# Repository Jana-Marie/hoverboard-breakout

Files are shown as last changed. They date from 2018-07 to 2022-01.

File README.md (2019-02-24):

# Hoverboard breakout boards

### [Bobbycar breakout](/bobbycar_breakout/)

Hoverboard breakout board for Bobbycars, features a PCB-Nunchuk connector, a linear regulator, pull-ups for I2C and pull-downs for ADC-input

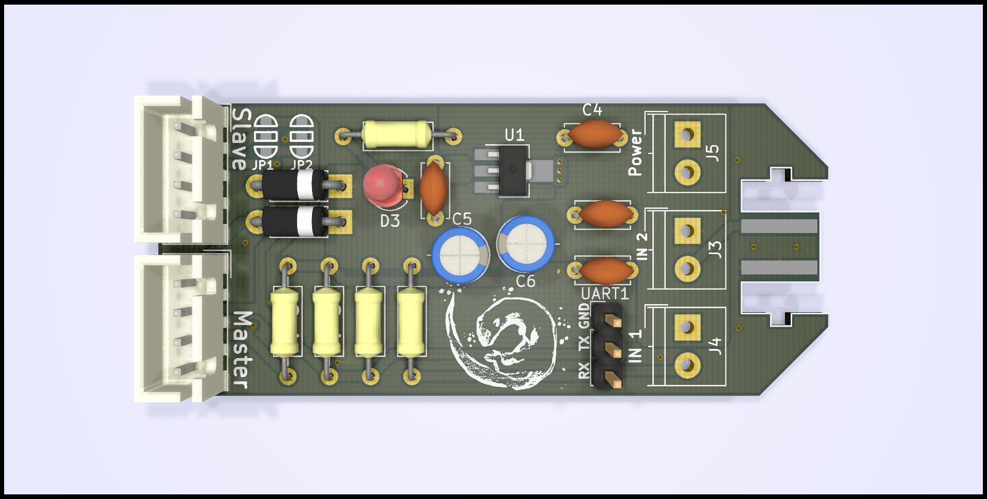
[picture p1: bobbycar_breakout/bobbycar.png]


### [Nunchuk breakout](/nunchuk_breakout/)

Nunchuk to hoverboard connector board, features a Nunchuk socket, a linear regulator and pullups. This board is only intended for nunchuk use, therefore it is smaller and features the fitting socket.

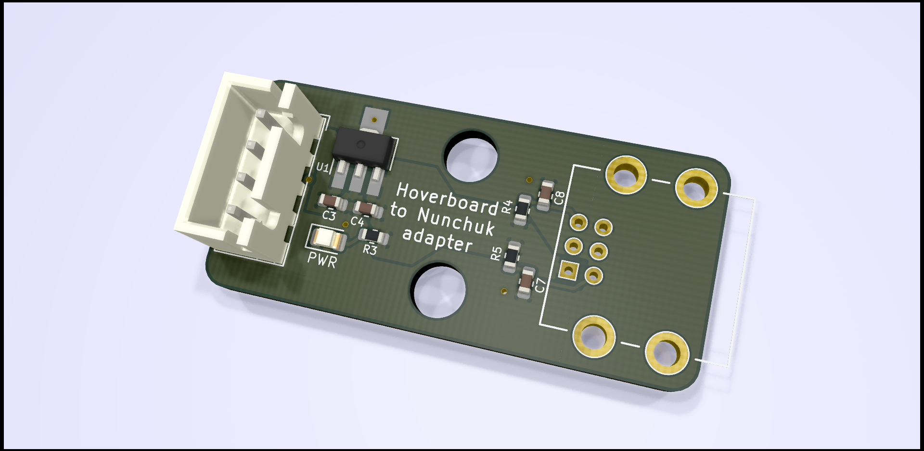
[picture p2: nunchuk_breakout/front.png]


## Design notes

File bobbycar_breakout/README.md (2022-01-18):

# hoverboard-breakout

Breakout board for hoverboard mainboards, it grands easy access to the boards uart, analog inputs PA2 and PA3 as well as I2C. It features a footprint for a generic 3.3V or 5V LDO (e.g. CJ78L05, L78L33ACUTR), 
screw terminals for the analog inputs, a power LED and a footprint for a nunchuck. 

Always mount the diode, the LED and the LDO. For I2C also two 3k3 pullups (labeled I2C) are mounted, for ADC you can add up to two pulldowns and filter capacitors.

The breakout board allows to connect two hoverboard mainbords. This can be done either to use them in parallel (e.g. route ADC to both) or to connect the two mainboards via UART. To connect the hoverboard mainboards in parallel, connect the middle pad of JP1 to the lower pad and the middle pad of JP2 to the upper pad. To connect the hoverboard mainboards via UART solder the pads of JP1 and JP2 the other way round.

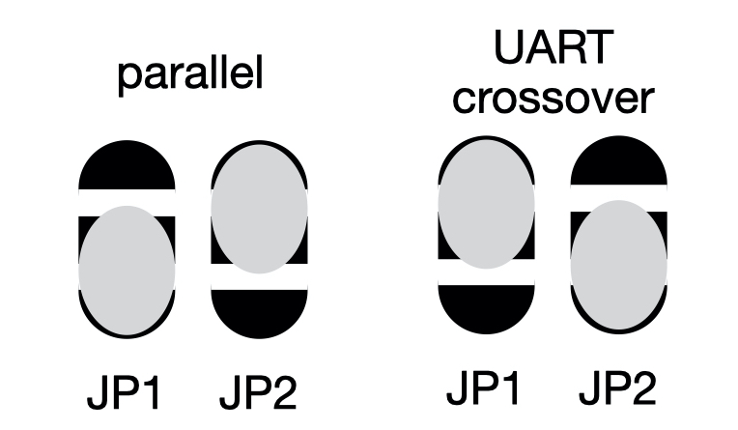
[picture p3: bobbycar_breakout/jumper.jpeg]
Jumper settings


Some of the resistors and capacitors can either be mounted with wired components or with smd components.

Frontview
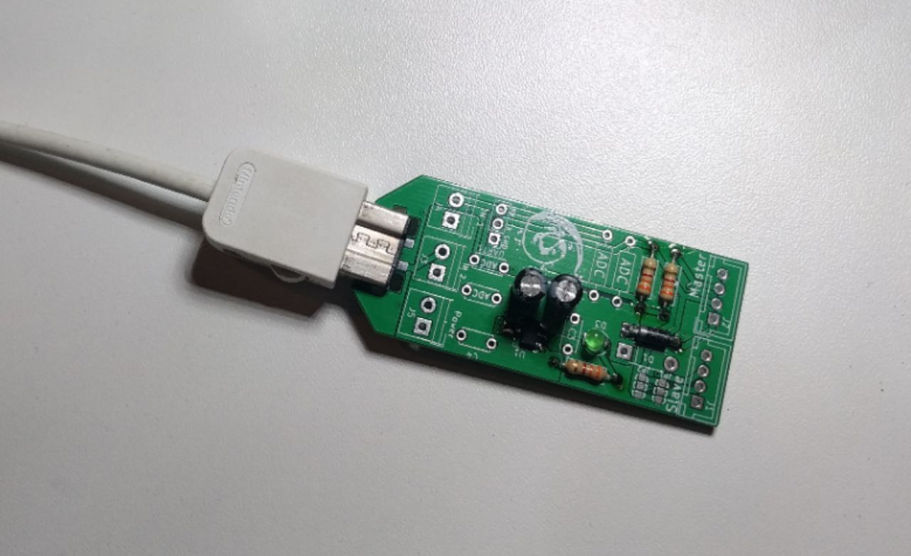
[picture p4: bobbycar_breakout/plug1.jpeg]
Plug1

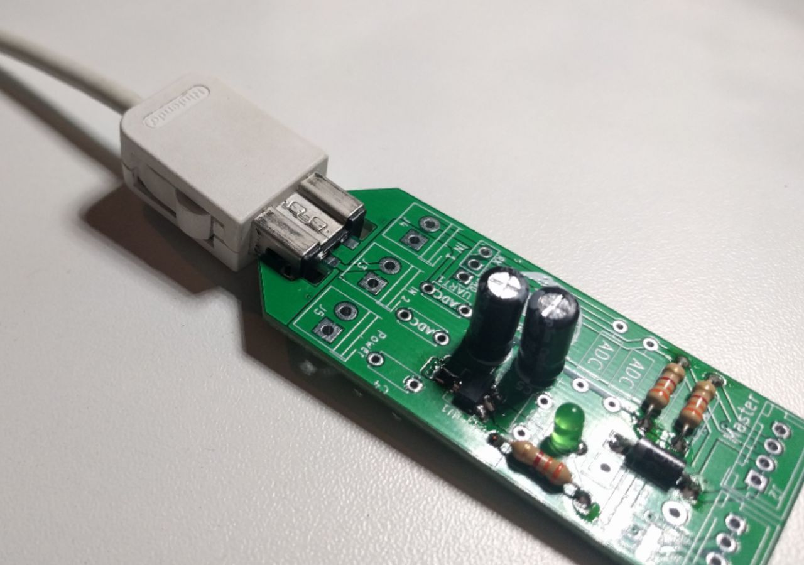
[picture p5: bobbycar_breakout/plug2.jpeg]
Plug2


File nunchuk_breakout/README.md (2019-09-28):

# hoverboard-nunchuk-breakout

Hoverboard to nunchuk-connector breakout.

Frontview
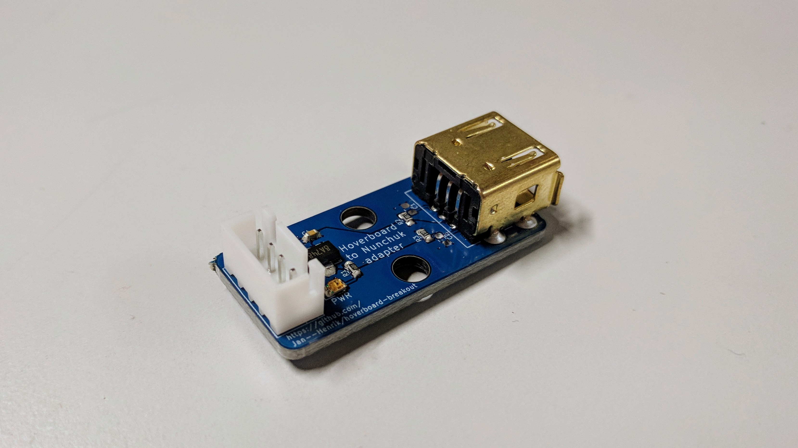
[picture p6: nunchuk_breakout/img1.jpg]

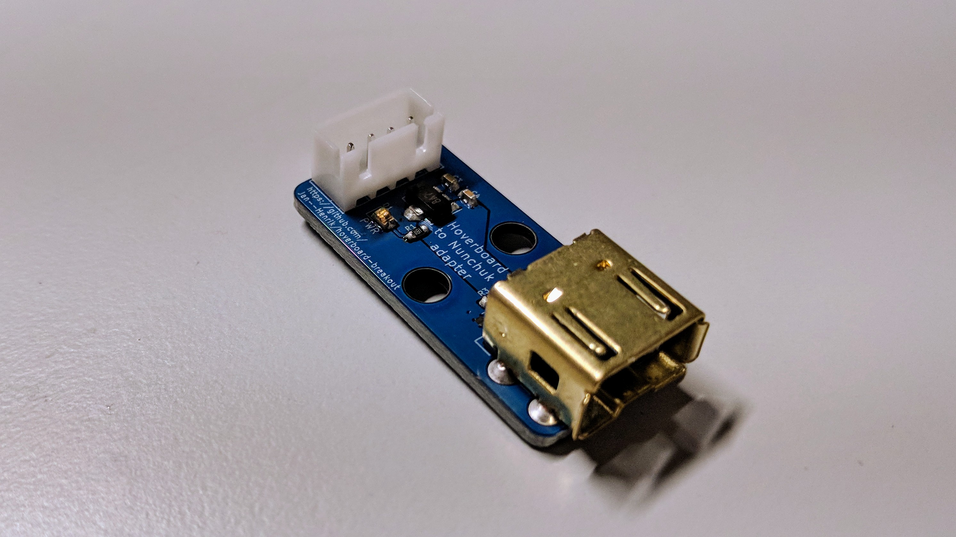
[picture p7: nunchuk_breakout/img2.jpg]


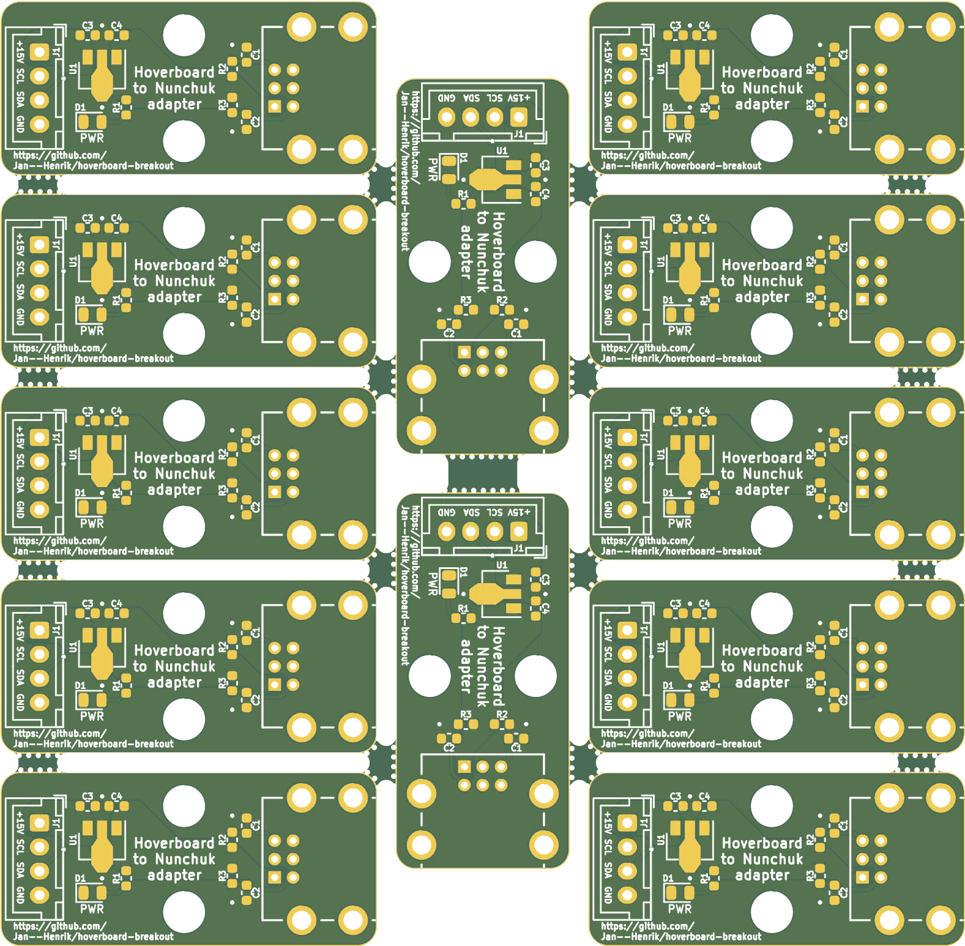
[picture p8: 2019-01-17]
nunchuk_breakout/gerber/panel/Nunchuk_breakout/nunchuk_breakout_Combined_Top.png

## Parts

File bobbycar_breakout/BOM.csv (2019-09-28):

References | Qty | Description | Manufacturer | MPN | Manufacturer | MPN | Manufacturer | MPN | Manufacturer | MPN | Manufacturer | MPN | Manufacturer | MPN | Manufacturer | MPN | Manufacturer | MPN | Manufacturer | MPN | Manufacturer | MPN | Manufacturer | MPN | Manufacturer | MPN | Digikey | Mouser | RS | Newark | Farnell
C2,C1 | 2 | 100nF C_Disc_D5.0mm_W2.5mm_P5.00mm | Murata | GRM155R71C104KA88D | Kemet | C0603C104K5RACTU | Yageo | CC0603KRX7R9BB104 | Murata | GRM188R71H104KA93D | Yageo | CC0805KRX7R9BB104 | Murata | GRM21BR71H104KA01L |  |  |  |  |  |  |  |  |  |  |  |  | 490-3261-1-ND | 80C0603C104K5R7867 | 7235228 | 72J5992 | 1288255
C3,C4 | 2 | 1uF C_Disc_D5.0mm_W2.5mm_P5.00mm | Yageo | CC0402KRX5R5BB105 | Murata | GRM155R60J105KE19D | Yageo | CC0603KRX7R8BB105 | Murata | GRM188R71E105KA12D | Yageo | CC0805KKX7R8BB105 | Murata | GRM21BR71H105KA12L | AVX | TAJA105K035RNJ |  |  |  |  |  |  |  |  |  |  | 490-1320-6-ND | 81GRM155R60J105KE19 | 7235180 | 68R4627 | 1845729
R2,R1 | 2 | DNP |  |  |  |  |  |  |  |  |  |  |  |  |  |  |  |  |  |  |  |  |  |  |  |  | CHF2010DNP500LXE-ND
R7,R6 | 2 | DNP |  |  |  |  |  |  |  |  |  |  |  |  |  |  |  |  |  |  |  |  |  |  |  |  | CHF2010DNP500LXE-ND
C7,C8 | 2 | DNP
D1,D2 | 2 | 1N400x D_DO-41_SOD81_P7.62mm_Horizontal
U1 | 1 | 78L33ACUTR |  |  |  |  |  |  |  |  |  |  |  |  |  |  |  |  |  |  |  |  |  |  |  |  | 497-1200-1-ND | 511L78L33ACU | 6869426 | 89K1361 | 2253467
UART1 | 1 | DNP |  |  |  |  |  |  |  |  |  |  |  |  |  |  |  |  |  |  |  |  |  |  |  |  | SIP32402ADNP-T1GE4CT-ND | 595OPT3004DNPR | 8908794 | 49Y4368 | 9289658
R3 | 1 | 220Ohm R_Axial_DIN0207_L6.3mm_D2.5mm_P10.16mm_Horizontal | Yageo | RC0603FR-07220RL | Panasonic | ERJ-3EKF2200V | Vishay | CRCW0603220RFKEA |  |  |  |  |  |  |  |  |  |  |  |  |  |  |  |  |  |  | 311-220HRDKR-ND | 667ERJ3EKF2200V | 8206802 | 64R5328 | 9238409
R4,R5 | 2 | 3k3 R_Axial_DIN0207_L6.3mm_D2.5mm_P10.16mm_Horizontal | Yageo | RC0402FR-073K3L | Panasonic | ERJ-2RKF3301X | Vishay | CRCW04023K30FKED | Yageo | RC0402FR-073K3L | Panasonic | ERJ-2RKF3301X | Vishay | CRCW04023K30FKED | Yageo | RC0402FR-073K3L | Panasonic | ERJ-2RKF3301X | Vishay | CRCW04023K30FKED | Yageo | RC0402FR-073K3L | Panasonic | ERJ-2RKF3301X | Vishay | CRCW04023K30FKED | P3.30KLCT-ND | 71CRCW04023.3KE3 | 6789263 | 64R5278 | 2302691
C5,C6 | 2 | 22uF CP_Radial_D5.0mm_P2.00mm | Murata | GRM21BR60J226ME39L | AVX | TAJB226K016RNJ | Panasonic | ECA-1HM220 |  |  |  |  |  |  |  |  |  |  |  |  |  |  |  |  |  |  | 490-1719-1-ND | 81GRM21R60J226ME39L | 7236029 | 24R6338 | 1735531
J1,J2 | 2 | B04B-XH-A
J4,J5,J3 | 3 | DNP |  |  |  |  |  |  |  |  |  |  |  |  |  |  |  |  |  |  |  |  |  |  |  |  | SIP32402ADNP-T1GE4CT-ND | 595OPT3004DNPR | 8908794 | 49Y4368 | 9289658
D3 | 1 | LED LED_D3.0mm
JP1,JP2 | 2 | DNP |  |  |  |  |  |  |  |  |  |  |  |  |  |  |  |  |  |  |  |  |  |  |  |  | SIP32402ADNP-T1GE4CT-ND | 595OPT3004DNPR | 8908794 | 49Y4368 | 9289658
J6 | 1 | NUNCHUK

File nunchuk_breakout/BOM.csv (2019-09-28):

References | Qty | Description | Manufacturer | MPN | Manufacturer | MPN | Manufacturer | MPN | Digikey | Mouser | RS | Newark | Farnell
U1 | 1 | 78L33ACUTR SOT-89 |  |  |  |  |  |  | 497-1200-1-ND | 511L78L33ACU | 6869426 | 89K1361 | 2253467
D1 | 1 | LED blue 0805
R1 | 1 | 220Ohm 0603 | Yageo | RC0603FR-07220RL | Panasonic | ERJ-3EKF2200V | Vishay | CRCW0603220RFKEA | 311-220HRDKR-ND | 667ERJ3EKF2200V | 8206802 | 64R5328 | 9238409
R2,R3 | 2 | 3.3kOhm 0603 | Yageo | RC0402FR-073K3L | Panasonic | ERJ-2RKF3301X | Vishay | CRCW04023K30FKED | P3.30KLCT-ND | 71CRCW04023.3KE3 | 6789263 | 64R5278 | 2302691
C3,C4 | 2 | 100nF 0603 | Yageo | CC0603KRX7R9BB104 | Murata | GRM188R71H104KA93D |  |  | 490-1519-6-ND | 603CC603KRX7R9BB104 | 7235676 | 68R4788 | 8820023
J1 | 1 | B4B-XH-A(LF)(SN) |  | https://lcsc.com/product-detail/_JST-Sales-America_B4B-XH-A-LF-SN_JST-Sales-America-B4B-XH-A-LF-SN_C144395.html |  |  |  |  | 455-2249-ND |  | 8201551P | 73M9436 | 1516278
NUNCHUK | 1 | NUNCHUK
C1,C2 | 2 | DNP |  | https://de.aliexpress.com/store/product/2PCS-Replacement-Jack-Socket-Dock-Connector-Port-for-Nintendo-Wii-Right-Left-Socket-Link-Controller/3084037_3288174986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

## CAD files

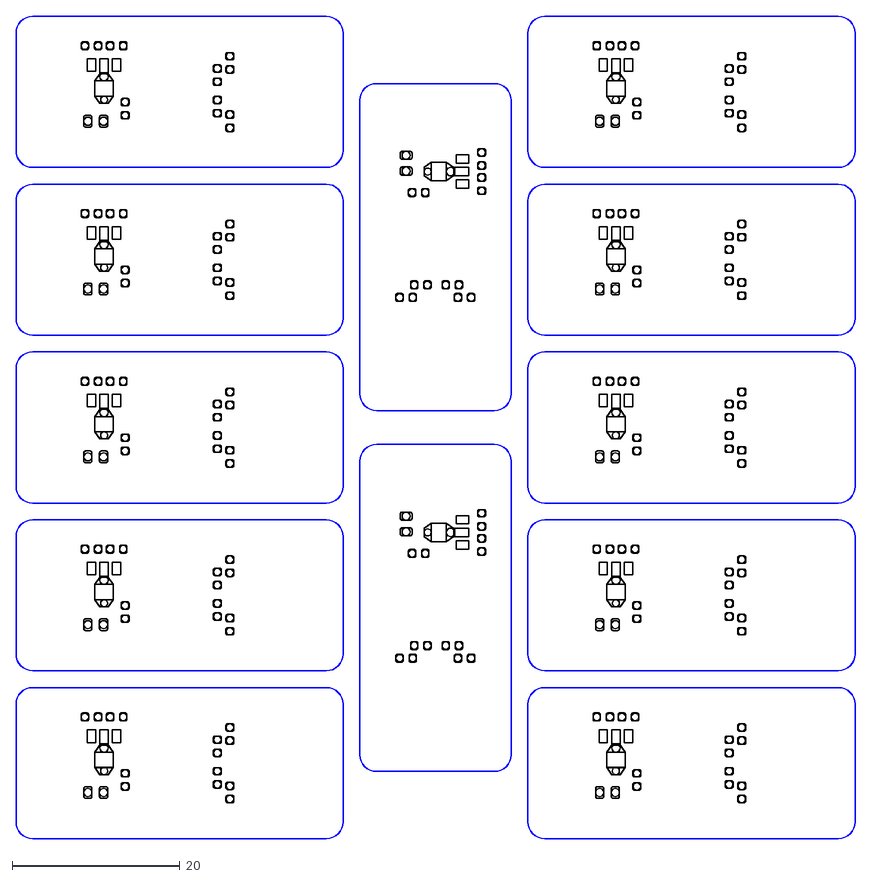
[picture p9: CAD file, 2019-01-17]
nunchuk_breakout/gerber/panel/Nunchuk_breakout/stencil.dxf
100.0 x 98.0

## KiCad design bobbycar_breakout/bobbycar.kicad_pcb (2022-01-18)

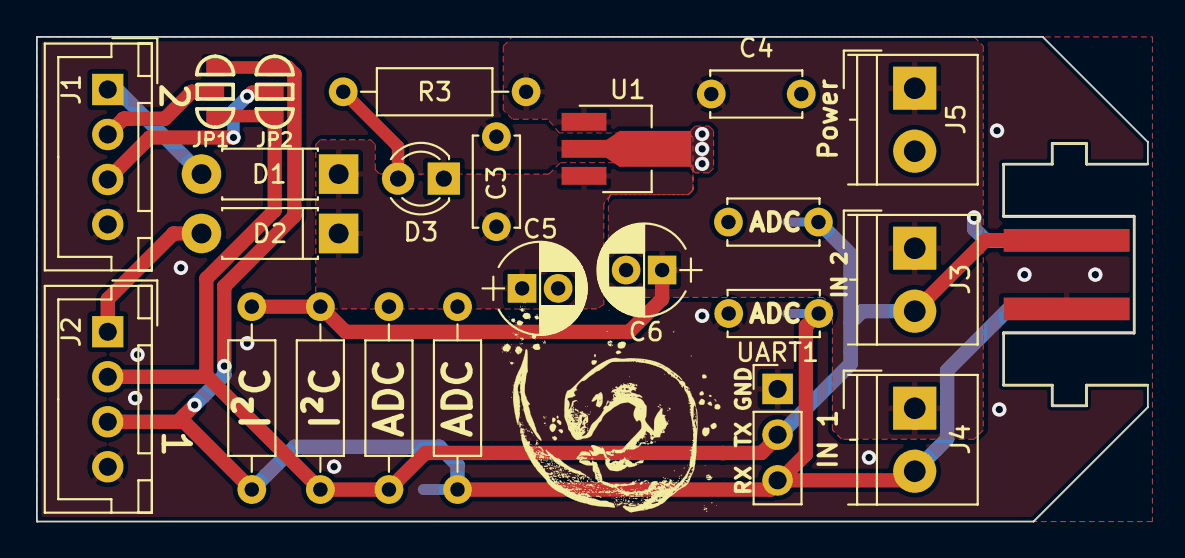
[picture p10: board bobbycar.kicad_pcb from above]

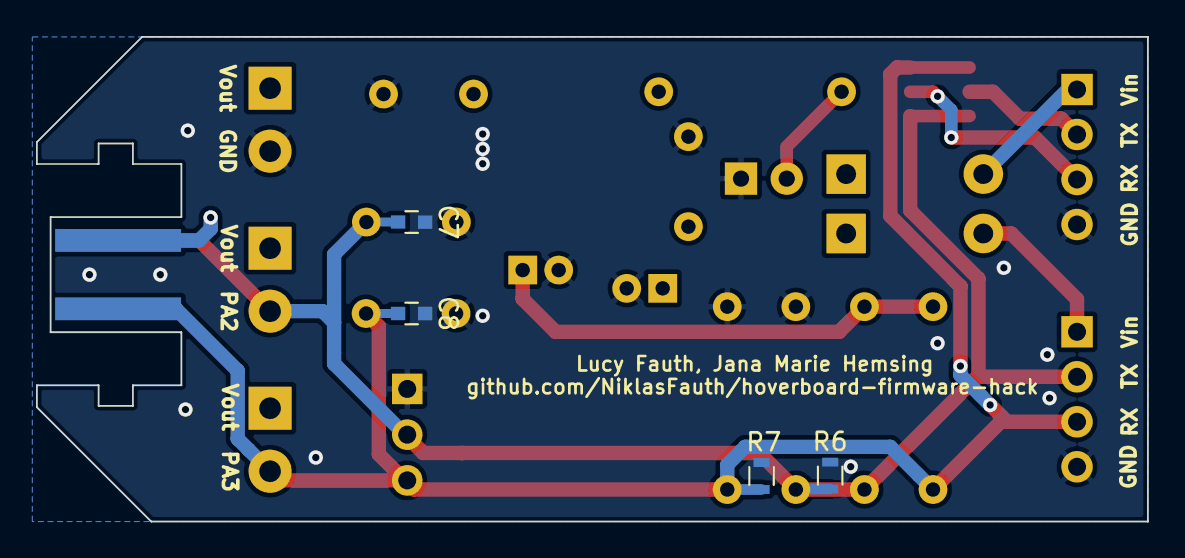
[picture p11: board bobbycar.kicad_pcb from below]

Board: 2 copper layers, 61.7 x 26.9 mm, 28 parts (4 on the bottom side), 10 nets.

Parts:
C1, C2: C_Small; C_Disc_D5.0mm_W2.5mm_P5.00mm
C3, C4: 1uF; C_Disc_D5.0mm_W2.5mm_P5.00mm
C5, C6: 22uF; CP_Radial_D5.0mm_P2.00mm
C7, C8: C_Small; C_0603
D1, D2: D; D_DO-41_SOD81_P7.62mm_Horizontal
D3: LED; LED_D3.0mm
J1, J2: Conn_01x04; JST_XH_B04B-XH-A_04x2.50mm_Straight
J3, J4, J5: Screw_Terminal_01x02; TerminalBlock_4UCON_19963_02x3.5mm_Straight
J6: Conn_01x04; NUNCHUCK
JP1, JP2: Jumper_NC_Dual; SOLDER-JUMPER_2-WAY
R1, R2: R_Small; R_Axial_DIN0207_L6.3mm_D2.5mm_P10.16mm_Horizontal
R3: 220Ohm; R_Axial_DIN0207_L6.3mm_D2.5mm_P10.16mm_Horizontal
R4, R5: 3k3; R_Axial_DIN0207_L6.3mm_D2.5mm_P10.16mm_Horizontal
R6, R7: R_Small; R_0603
U1: L7805SOT89; SOT-89-3_Handsoldering
UART1: Conn_01x03; Pin_Header_Straight_1x03_Pitch2.54mm

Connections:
GND: C1.1, C2.2, C3.2, C4.2, C5.2, C6.2, C7.1, C8.2, D3.1, J1.4, J2.4, J5.2, J6.1, R1.1, R2.2, R6.1, R7.2, U1.2, UART1.1
unnamed: D1.2, J1.1
unnamed: D2.2, J2.1
unnamed: D3.2, R3.1
RX: C2.1, C8.1, J2.3, J4.2, J6.4, JP1.3, JP2.3, R2.1, R4.2, R7.1, UART1.3
RX.1: J1.3, JP2.2
TX: C1.2, C7.2, J2.2, J3.2, J6.2, JP1.1, JP2.1, R1.2, R5.2, R6.2, UART1.2
TX.1: J1.2, JP1.2
VCC: C4.1, C6.1, J3.1, J4.1, J5.1, J6.3, R3.2, R4.1, R5.1, U1.1
VDD: C3.1, C5.1, D1.1, D2.1, U1.3

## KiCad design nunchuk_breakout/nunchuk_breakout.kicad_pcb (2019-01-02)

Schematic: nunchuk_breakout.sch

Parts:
C1, C2: 10p; C_0603_1608Metric
C3, C4: 1uF; C_0603_1608Metric
D1: LED; LED_0805_2012Metric
H1, H2: MountingHole; MountingHole_4.3mm_M4
J1: Conn_01x04; JST_XH_B04B-XH-A_1x04_P2.50mm_Vertical
P1: CONN_WII
R1: 220Ohm; R_0603_1608Metric
R2, R3: 3k3; R_0603_1608Metric
U1: L78L33_SOT89; SOT-89-3

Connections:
GND: C1.2, C2.1, C3.2, C4.2, D1.1 (K), J1.4, P1.6, U1.2 (GND)
unnamed: D1.2 (A), R1.1
SCL: C2.2, J1.2, P1.2, R3.2
SDA: C1.1, J1.3, P1.5, R2.2
VCC: C4.1, P1.1, R1.2, R2.1, R3.1, U1.1 (OUT)
VDD: C3.1, J1.1, U1.3 (IN)

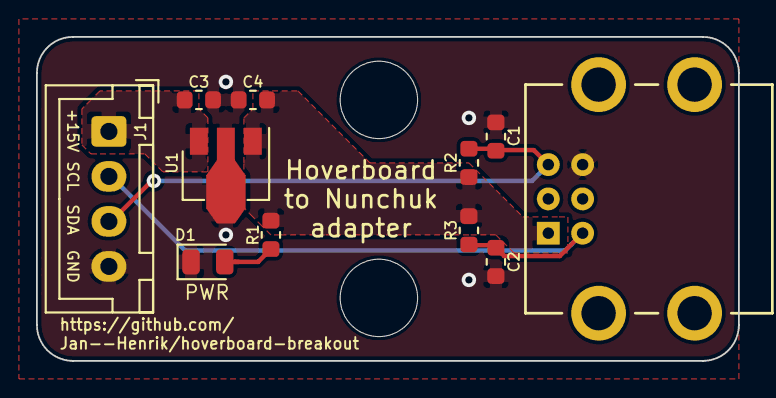
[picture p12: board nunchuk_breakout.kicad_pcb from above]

Board: 2 copper layers, 39.0 x 18.0 mm, 13 parts (0 on the bottom side), 6 nets.

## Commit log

2018-04-16 added KiCAD project files
    [bobbycar.kicad_pcb, bobbycar.sch]
2018-04-16 added gerber files
    [bobbycar-B.Cu.gbr, bobbycar-B.Mask.gbr, bobbycar-B.Paste.gbr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]
2018-06-26 UPDATED pcb files
    [bobbycar.kicad_pcb, bobbycar.sch]
2018-08-13 added gerber
    [bobbycar-B.Cu.gbr, bobbycar-B.Mask.gbr, bobbycar-B.Paste.gbr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]
2018-08-13 added BOM
    [BOM.csv]
2018-09-22 fixed library names
    [bobbycar.sch]
2019-01-02 moved V1 to V1 folder
    [BOM.csv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]
2019-01-02 added V2
    [nunchuk_breakout-B.Cu.gbl, nunchuk_breakout-B.Mask.gbs, nunchuk_breakout-B.Paste.gbp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]
2019-01-02 renamed folders
    [BOM.csv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]
2019-01-02 moved kicad lib
2019-01-02 added image
    [nunchuk_breakout.kicad_pcb]
2019-01-02 updated gerber
    [nunchuk_breakout-B.Cu.gbl, nunchuk_breakout-B.Mask.gbs, nunchuk_breakout-B.Paste.gbp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]
2019-01-02 updated PCB
    [nunchuk_breakout.kicad_pcb]
2019-01-02 changed rendering
    [nunchuk_breakout-B.Cu.gbl, nunchuk_breakout-B.Mask.gbs, nunchuk_breakout-B.Paste.gbp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]
2019-01-17 added panelized gerber (12/panel)
    [combined.GKO, combined.drl, combined.gbl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]
2019-02-24 added x3 gerber
2019-05-24 Fix bom csv headers for correct parsing
    [BOM.csv]
2019-09-28 updated bom
    [BOM.csv]
2020-08-22 Add kicad_pcb files to kitspace.yaml
2021-03-11 Remove duplicate gerber files
    [bobbycar-B.Cu.gbl, bobbycar-B.Mask.gbs, bobbycar-B.Paste.gbp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]
2022-01-18 updated to kicad 6
    [bobbycar-B_Cu.gbr, bobbycar-B_Mask.gbr, bobbycar-B_Paste.gbr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]
2022-10-03 Kitspace: have nunchuk panel and non-panel projects
    [nunchuk_breakout-B.Cu.gbl, nunchuk_breakout-B.Mask.gbs, nunchuk_breakout-B.Paste.gbp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]
